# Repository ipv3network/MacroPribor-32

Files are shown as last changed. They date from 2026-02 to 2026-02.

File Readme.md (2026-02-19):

# MacroPribor-32
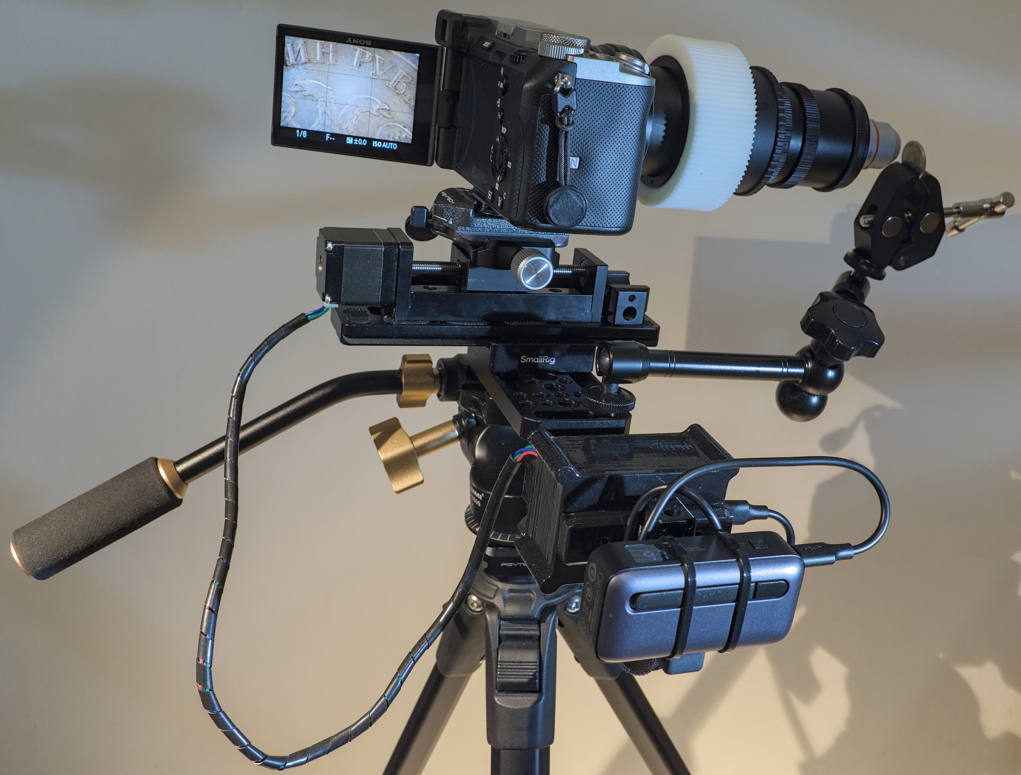
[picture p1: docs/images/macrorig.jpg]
macrorig

Это проект по созданию самодельной моторизованной рейки, облегчающей процесс съемки серий кадров для последующего фокус-стекинга.

Моторизованная направляющая перемещается в заданную начальную точку, сдвигает камеру на небольшие расстояния и посылает камере сигналы для съемки по BLE (Bluetooth Low Energy), пока не достигнет заданной конечной точки. Весь процесс контролируется через встроенный в контроллер веб-интерфейс.

В данный момент поддерживаются только камеры Sony, совместимые с пультом RMT-P1BT (например: A7III, A7V, A7C, A6700, A9III и т.д.).

Код для работы с BLE основан на [https://github.com/coral/freemote](https://github.com/coral/freemote) и [https://github.com/dzwiedziu-nkg/esp32-a7iv-rc](https://github.com/dzwiedziu-nkg/esp32-a7iv-rc).

Всё собрано из недорогих и доступных в продаже компонентов. Корпус с электронными модулями напечатан на 3D-принтере, но при желании (и отсутствии 3D-принтера) можно изготовить корпус альтернативными способами или обойтись вообще без него.

Проект в стадии не очень активной разработки. В будущем планируется разработать нормальный дизайн печатной платы и корпуса, добавить совместимость с другими моделями камер (в том числе по проводному разъему для пульта) и не только это.

## Содержание
* [Инструкция по сборке](#инструкция-по-сборке)
    * [Список компонентов](#список-компонентов)
    * [Сборка электроники](#сборка-электроники)
    * [Сборка корпуса и механических частей](#сборка-корпуса-и-механических-частей)
    * [Установка прошивки](#установка-прошивки)
* [Использование](#использование)
    * [Подключение к камере](#подключение-к-камере)
    * [Настройка сети](#настройка-сети)

# Инструкция по сборке

## Список компонентов
<details>
<summary>Примерный список компонентов на Али с ценами на февраль 2026 года (раскрыть картинку)</summary>
Можно уложиться в 5к рублей.

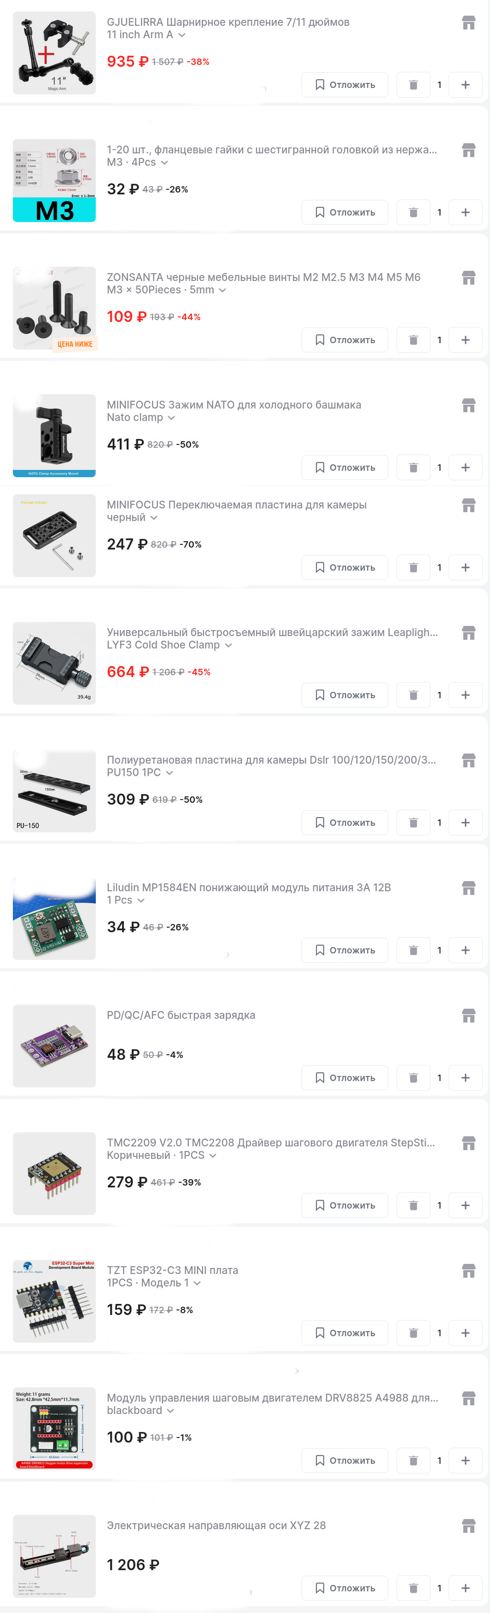
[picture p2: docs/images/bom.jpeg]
bom

</details>

**Электроника** (сложно сказать, по каким ключевым словам конкретные модули найдутся на маркетплейсе, но вы можете визуально ориентироваться по картинкам):
* [Линейная направляющая](./docs/images/rail.jpg) (актуатор) с шаговым двигателем NEMA11, винтовой передачей и рельсовой направляющей. Можно найти в продаже по запросам: "мини направляющая чпу", "электрическая направляющая оси", "линейная направляющая ось чпу" и т.п. Насколько я понимаю, на них стоит дешевый китайский аналог дорогого китайского двигателя MOON'S LE111S-W0601-50-AR1-S-100.
* ESP32-C3 Super Mini (как на схеме ниже).
* Драйвер шагового двигателя (A4988, DRV8825, TMC2209 и т.п.).
* Плата расширения драйвера шагового двигателя (как на схеме ниже).
* Type-C PD/QC триггер (как на схеме ниже).
* Понижающий DC-DC преобразователь MP1584EN или что-то аналогичное.
* Диод Шоттки 1N5819.
* Провода.
* Набор JST коннекторов и обжимка. Но это не обязательно, можно просто припаять провода к платам.

**Крепежные элементы**:
* [Площадка Arca Swiss PU-150](./docs/images/arcaplate.jpg).
* Зажим Arca Swiss, в котором можно просверлить крепежные отверстия под каретку направляющей (смотри схему с размерами ниже).
* Винты М3 для крепления площадки и зажима Arca Swiss к моторизованной направляющей — 8 штук. Длину нужно подобрать эмпирическим путём.
* Гайки М3 — 4 штуки. Лучше с фланцем, но подойдут и обычные.
* Винты для компьютерных корпусных кулеров для сборки 3D-печатного корпуса — 10 штук.
* Сырная пластина, Magic Arm, зажим для NATO rail и прочие необязательные вещи для удобного крепления.
 
## Сборка электроники
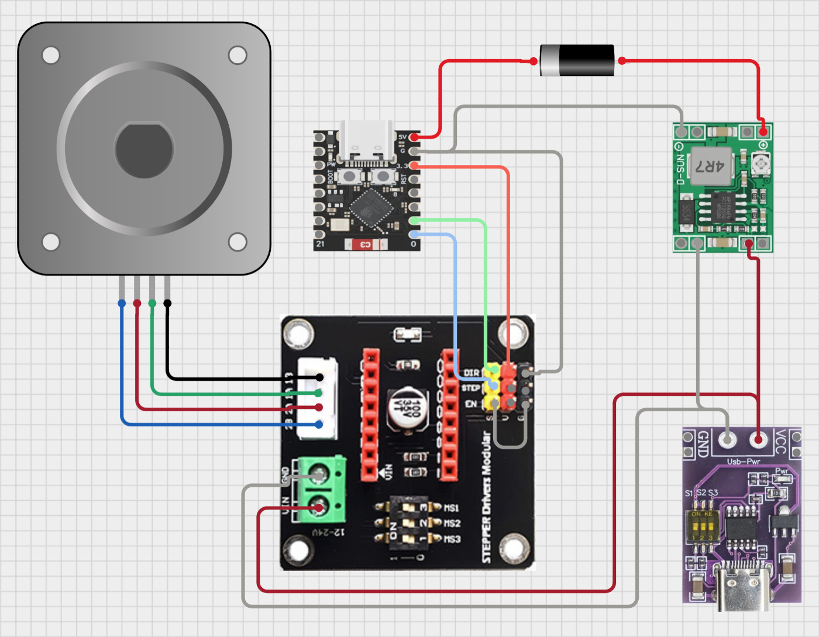
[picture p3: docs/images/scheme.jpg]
scheme

1. Настройте микропереключателями на Type-C PD/QC триггере выходное напряжение в диапазоне от 12В до 20В. Убедитесь, что все нужные блоки питания/зарядные устройства/повербанки выдают нужное напряжение с этими настройками модуля. Некоторые девайсы могут отказаться выдавать определенное напряжение из-за их конструктивных особенностей реализации PD/QC протокола.
2. Подключите выход питания из Type-C триггера ко входу модуля DC-DC преобразователя MP1584EN. 
3. Подайте питание. 
4. Подстроечным резистором настройте на нем выходное напряжение 5В.
5. Отключите питание.
6. Установите драйвер шагового двигателя в плату расширения. Настройте нужные параметры микрошага переключателями на плате расширения. Настройки зависят от модели драйвера, их можно посмотреть в документации драйвера.
7. Замкните перемычкой контакты EN и GND на плате расширения драйвера двигателя.
8. Подключите микроконтроллерный модуль ESP32-C3 к стабилизатору напряжения и драйверу двигателя по схеме.
9. Подключите питание **с отключенным от платы двигателем** и подстроечным резистором на плате драйвера настройте референсное напряжение Vref (напряжение между корпусом подстроечного резистора и GND), соответствующее ограничению тока в 500мА. Ограничение тока вычисляется по формуле из документации, для каждой модели драйвера формула своя. Например, для DRV8825 ``Vref = Current Limit / 2``, т.е. для тока 0.5А значение Vref должно быть 0.25В.
10. Подключите двигатель.

## Сборка корпуса и механических частей
Просверлите отверстия сверлом 3 мм в зажиме и площадке Arca Swiss по размерам со схемы ниже. Прикрутите их к направляющей.
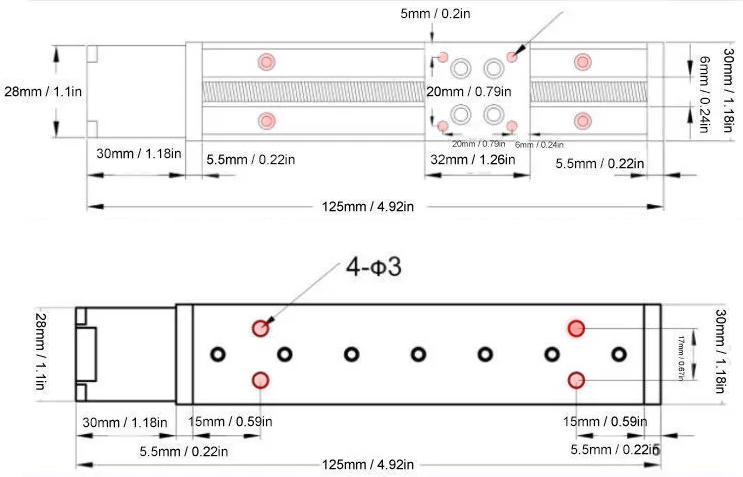
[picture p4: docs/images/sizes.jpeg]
size


У меня был немного неподходящий зажим. Но он уже был, и его не пришлось покупать специально. Поэтому пришлось доработать фрезером.
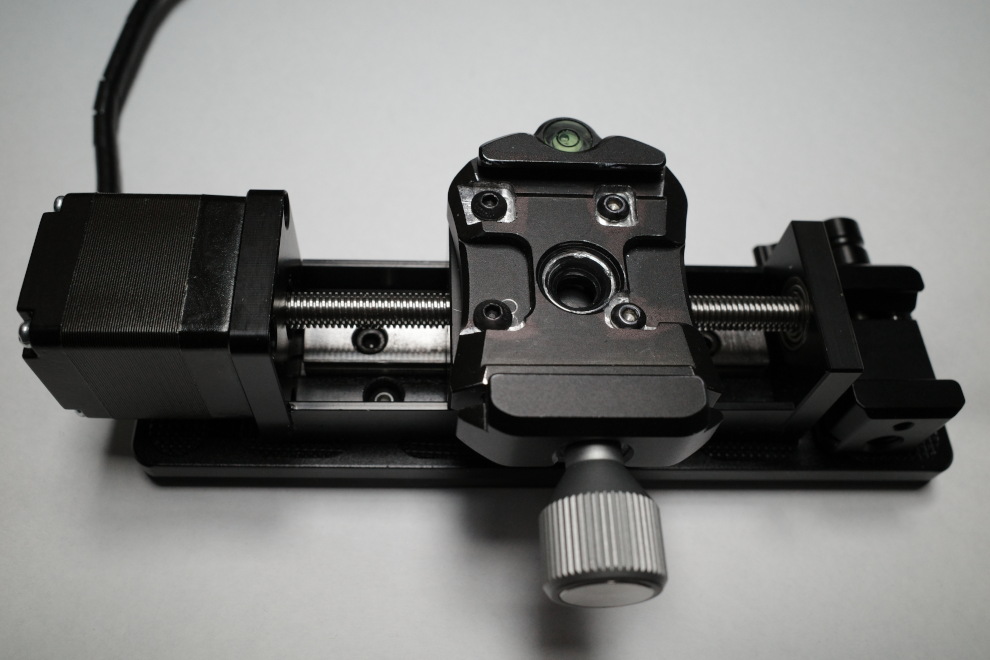
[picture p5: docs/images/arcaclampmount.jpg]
arcaclampmount

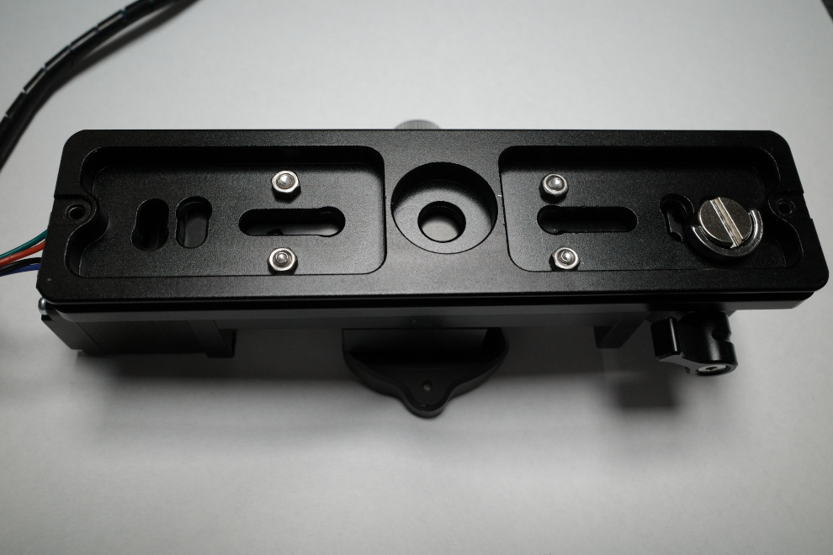
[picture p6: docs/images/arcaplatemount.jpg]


Type-C PD/QC триггер жестко фиксируется в корпусе и прикручивается крышкой с четырьмя винтами от корпусных вентиляторов. Дизайн крепления основан на [этой модели](https://www.printables.com/model/928729-pdqcafc-decoy-trigger-module-enclosure). И провода должны быть припаяны к нему [аналогичным образом](./docs/images/typecdecoy.jpg).

В монтажные отверстия на модулях я запаял JST колодки на плату и обжал на проводах JST разъемы. На гребенку платы для драйвера двигателя установил провода с обжатыми контактами от JST под термоусадкой. После укладки плат зафиксировал их термоклеем. Получилось не очень красиво, но приемлемо.

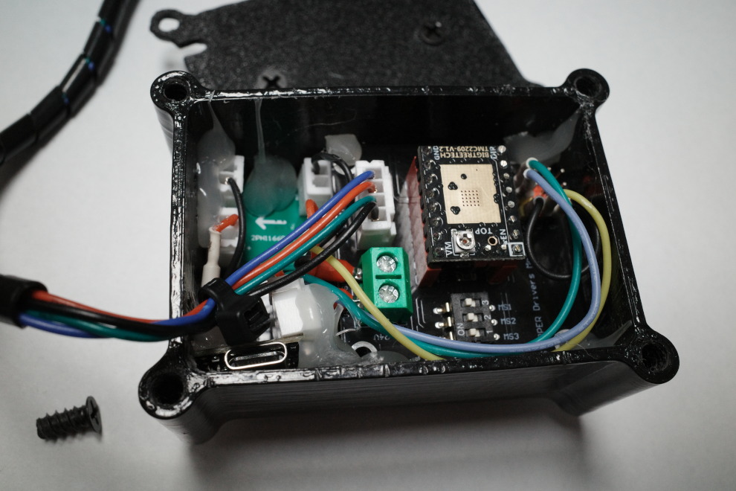
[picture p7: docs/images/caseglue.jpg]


## Установка прошивки
1. Установите PlatformIO и esptool.
2. Отключите питание от Type-C триггера, подключите ESP32-C3 по USB к компьютеру.
3. Можно очистить флеш контроллера:
```bash
pio run --target erase
```
4. В файле ``src/main.cpp`` найдите строку:
```C++
#define CAMERA_NAME "ILCE-7C"  // Имя камеры в Bluetooth меню
```
и замените название модели на вашу.

5. В каталоге со склонированным репозиторием запустите:
```bash
pio run # сборка
pio run --target upload # заливка прошивки
pio run --target uploadfs # заливка файловой системы
```
6. После успешной [настройки сети](#настройка-сети) можно обновлять прошивку по сети через OTA:
```bash
pio run -t clean -e ota
pio run -e ota --target upload
pio run -e ota --target uploadfs
```

# Использование
Интерфейс должен быть интуитивно понятным.

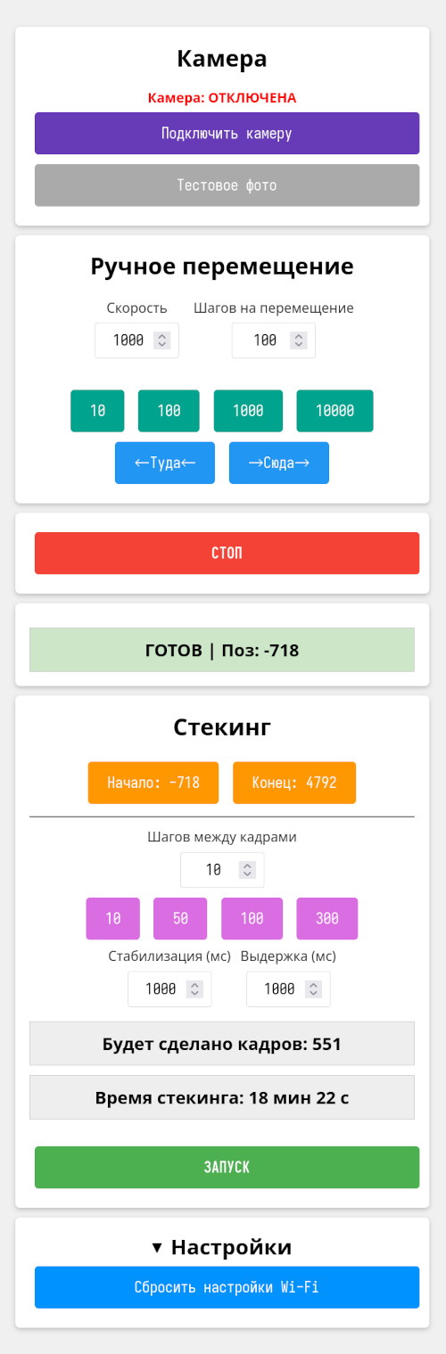
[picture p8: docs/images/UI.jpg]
UI


## Подключение к камере

В меню камеры следуйте инструкции по подключению пульта Sony RMT-P1BT.
Когда в камере запустите "Pairing", в веб-интерфейсе нажмите кнопку "Подключить камеру".

## Настройка сети

При первом включении контроллер поднимает точку доступа с названием "MacroPribor-32" и паролем "MacroPribor-32", если в его памяти до этого не были сохранены данные для подключения к точке доступа (обновление прошивки без предварительной полной очистки флеша не очищает настройки Wi-Fi). Подключайтесь к точке доступа "MacroPribor-32", переходите на её Captive portal [http://192.168.4.1](http://192.168.4.1), настраивайте вашу точку доступа.
Контроллер работает только с точками доступа на 2.4 ГГц, в её сети должен быть DHCP сервер, который выдаст IP адрес контроллеру.

Если нужно принудительно сбросить настройки Wi-Fi -- нажмите кнопку "Сбросить настройки Wi-Fi".

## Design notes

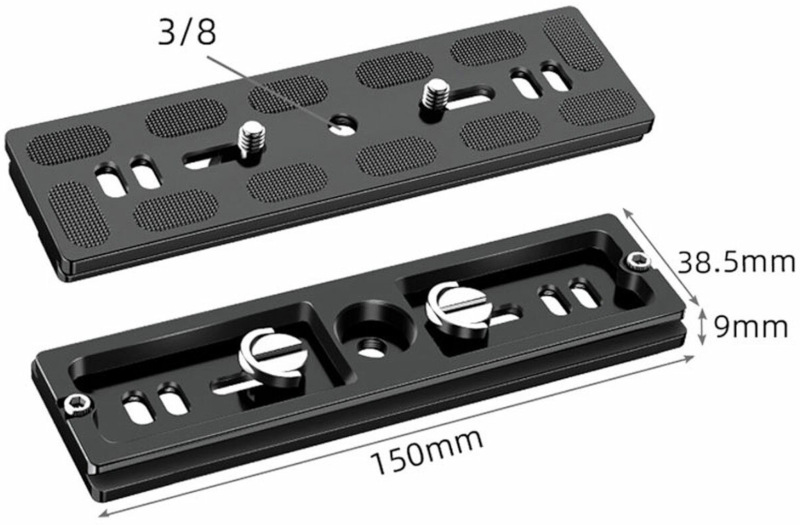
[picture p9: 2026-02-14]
docs/images/arcaplate.jpg

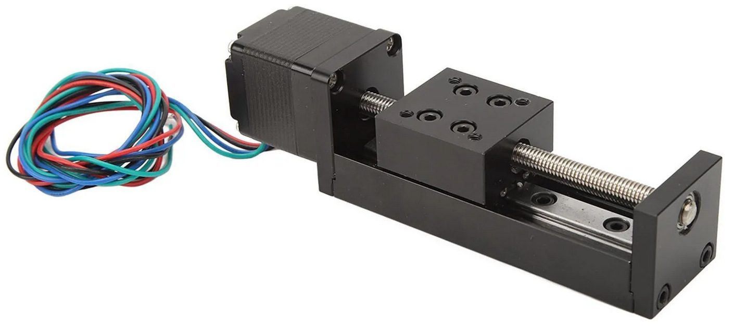
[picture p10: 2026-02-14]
docs/images/rail.jpg

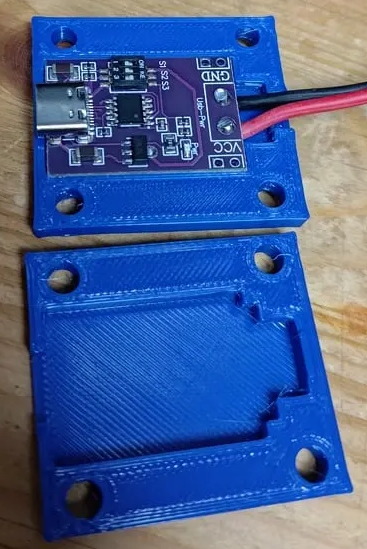
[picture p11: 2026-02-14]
docs/images/typecdecoy.jpg

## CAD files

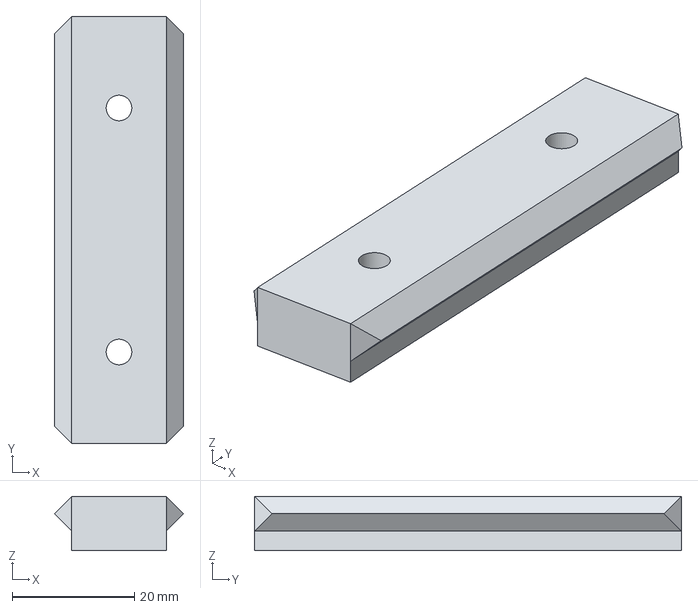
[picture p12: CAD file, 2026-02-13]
3d/electronics_enclosure-rail.step
21.2 x 70.0 x 8.90 mm

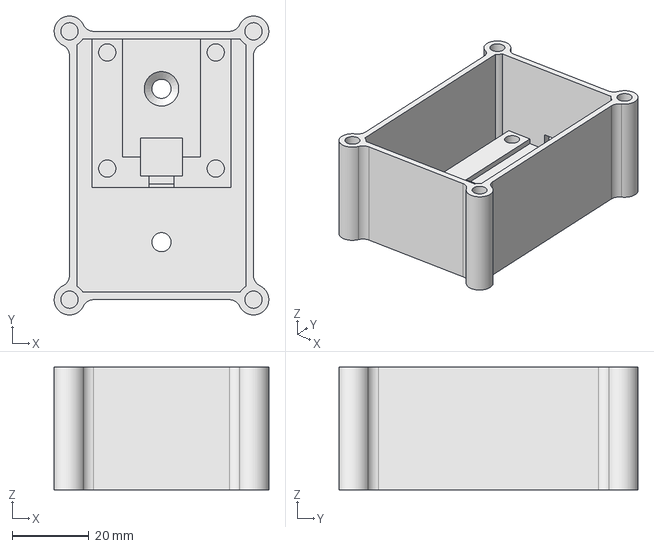
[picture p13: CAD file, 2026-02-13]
3d/electronics_enclosure-Down.step
56.0 x 78.0 x 32.0 mm

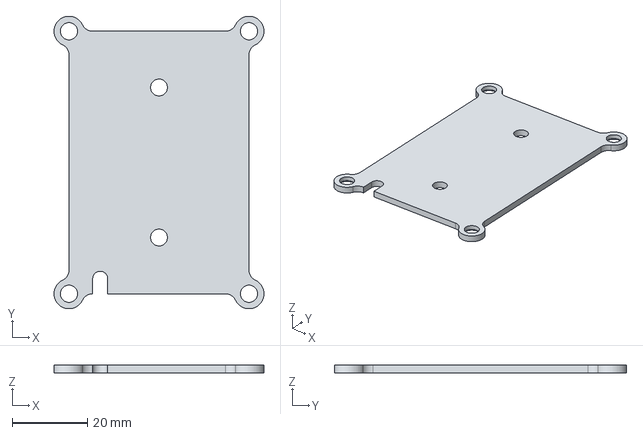
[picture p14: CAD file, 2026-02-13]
3d/electronics_enclosure-Up.step
56.0 x 78.0 x 2.00 mm

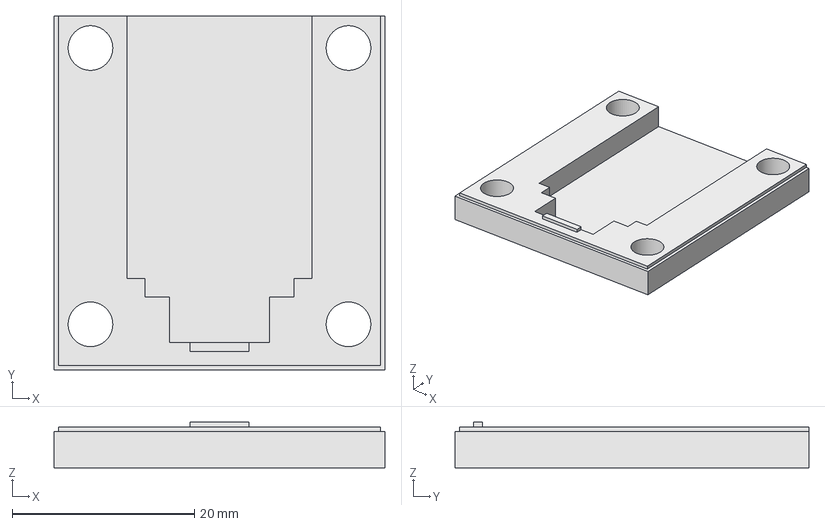
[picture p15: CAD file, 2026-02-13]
3d/electronics_enclosure-decoy_UP.step
36.3 x 38.8 x 5.00 mm

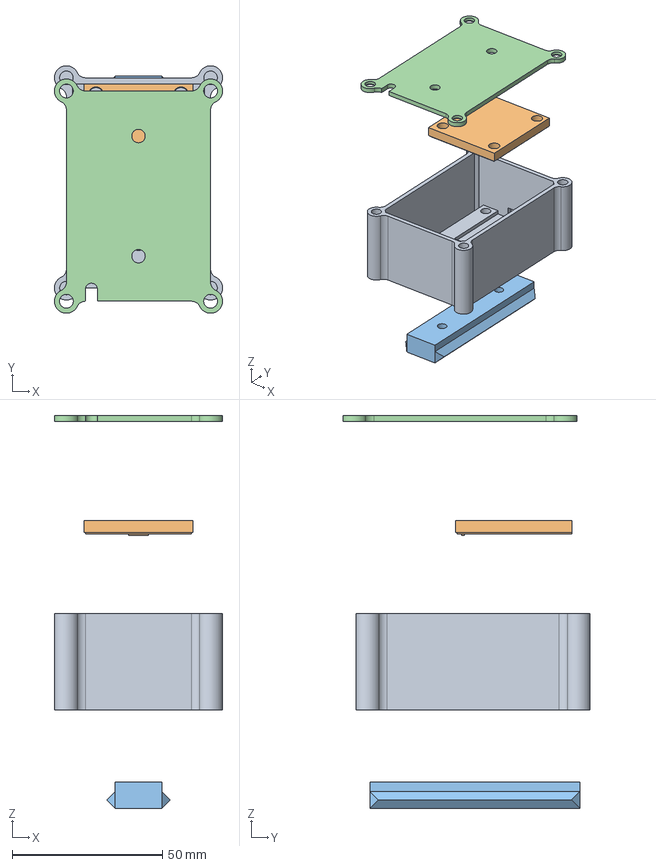
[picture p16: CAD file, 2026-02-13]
3d/electronics_enclosure.FCStd
56.0 x 82.4 x 130.9 mm
Down
decoy_UP
rail
Up

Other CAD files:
3d/electronics_enclosure-Down.stl
3d/electronics_enclosure-Up.stl
3d/electronics_enclosure-decoy_UP.stl
3d/electronics_enclosure-rail.stl

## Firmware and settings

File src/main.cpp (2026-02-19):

#include <WiFi.h>
#include <WiFiUdp.h>
#include <WiFiManager.h>
#include <ArduinoOTA.h>
#include <WebServer.h>
#include <FastAccelStepper.h>
#include <BLEDevice.h>
#include <LittleFS.h>

// ================= НАСТРОЙКИ СЕТИ =================
// Если не удается подключиться к ранее сохраненной точке доступа — поднимаем точку доступа "MacroPribor-32" с паролем "MacroPribor-32"
const char* APssid     = "MacroPribor-32";
const char* APpassword = "MacroPribor-32";
const char* Hostname   = "macropribor-32";

WiFiManager wifiManager;
WebServer      server(80);

// ================= НАСТРОЙКИ BLE (SONY) =================
#define CAMERA_NAME "ILCE-7C"  // Имя камеры в Bluetooth меню

// UUID сервисов Sony
static BLEUUID serviceUUID("8000FF00-FF00-FFFF-FFFF-FFFFFFFFFFFF");
static BLEUUID charCommandUUID((uint16_t)0xFF01);
static BLEUUID charNotifyUUID((uint16_t)0xFF02);

// Команды управления камерой
uint8_t HALF_DOWN[] = {0x01, 0x07};  // Половинное нажатие
uint8_t FULL_DOWN[] = {0x01, 0x09};  // Полное нажатие
uint8_t FULL_UP[]   = {0x01, 0x08};  // Отпустить
uint8_t HALF_UP[]   = {0x01, 0x06};  // Отпустить на половину

// ================= ПИНЫ МОТОРА =================
#define PIN_STEP 0
#define PIN_DIR 1

// ================= НАСТРОЙКИ МЕХАНИКИ =================
#define FIXED_ACCELERATION 1400
#define SPEED 5000

FastAccelStepperEngine engine  = FastAccelStepperEngine();
FastAccelStepper*      stepper = NULL;

// ================= ГЛОБАЛЬНЫЕ ПЕРЕМЕННЫЕ =================
long          pointA           = 0;
long          pointB           = 0;
bool          isStacking       = false;
int           stackState       = 0;
unsigned long stateTimer       = 0;
long          nextPos          = 0;
int           direction        = 1;
int           SHUTTER_PULSE_MS = 200;
uint32_t      last_ota_time    = 0;
bool          otaActive        = false;
// Параметры с веба
long web_speed          = 1000;
long web_stack_step     = 100;
long web_settle_delay   = 1000;
long web_exposure_delay = 1000;

// BLE Переменные
boolean                  bleConnected = false;
boolean                  doConnect    = false;
boolean                  doScan       = false;
BLEAddress*              pServerAddress;
BLERemoteCharacteristic* remoteCommand;
BLERemoteCharacteristic* remoteNotify;
BLEClient*               pClient;

// ================= BLE КЛАССЫ ОБРАТНОЙ СВЯЗИ =================

// Клиент подключился/отключился
class MyClientCallback : public BLEClientCallbacks {
    void onConnect(BLEClient* pclient) { Serial.println("BLE Connected!"); }
    void onDisconnect(BLEClient* pclient) {
        bleConnected = false;
        Serial.println("BLE Disconnected!");
    }
};

// Поиск устройств
class MyAdvertisedDeviceCallbacks : public BLEAdvertisedDeviceCallbacks {
    void onResult(BLEAdvertisedDevice advertisedDevice) {
        Serial.print("BLE Found: ");
        Serial.println(advertisedDevice.getName().c_str());

        // Ищем камеру по имени
        if (advertisedDevice.getName() == CAMERA_NAME) {
            advertisedDevice.getScan()->stop();
            pServerAddress = new BLEAddress(advertisedDevice.getAddress());
            doConnect      = true;
            doScan         = false;
            Serial.println("Camera Found! Ready to connect.");
        }
    }
};

// Спаривание
class MySecurityCallbacks : public BLESecurityCallbacks {
    uint32_t onPassKeyRequest() { return 123456; }
    void     onPassKeyNotify(uint32_t pass_key) {}
    bool     onSecurityRequest() { return true; }
    void     onAuthenticationComplete(esp_ble_auth_cmpl_t cmpl) {
        if (cmpl.success)
            Serial.println("Pairing Success");
        else
            Serial.println("Pairing Failed");
    }
    bool onConfirmPIN(uint32_t pin) { return true; }
};

// ================= ФУНКЦИИ BLE =================

bool connectToCamera() {
    Serial.print("Connecting to ");
    Serial.println(pServerAddress->toString().c_str());

    if (pClient->connect(*pServerAddress)) {
        Serial.println("Connected to server");

        BLERemoteService* pRemoteService = pClient->getService(serviceUUID);
        if (pRemoteService == nullptr) {
            Serial.println("Failed to find service UUID");
            return false;
        }

        remoteCommand = pRemoteService->getCharacteristic(charCommandUUID);
        remoteNotify  = pRemoteService->getCharacteristic(charNotifyUUID);

        if (remoteCommand == nullptr || remoteNotify == nullptr) {
            Serial.println("Failed to find characteristics");
            return false;
        }

        bleConnected = true;
        return true;
    }
    return false;
}

void triggerShutterBLE() {
    if (!bleConnected || remoteCommand == nullptr) return;

    remoteCommand->writeValue(HALF_DOWN, 2, true);
    delay(50);
    remoteCommand->writeValue(FULL_DOWN, 2, true);
}

void releaseShutterBLE() {
    if (!bleConnected || remoteCommand == nullptr) return;

    remoteCommand->writeValue(FULL_UP, 2, true);
    delay(50);
    remoteCommand->writeValue(HALF_UP, 2, true);
}

// ================= ЛОГИКА СЕРВЕРА =================

void handleRoot() {
    File indexHTML = LittleFS.open("/index.html", "r");
    if (!indexHTML) {
        server.send(500, "text/plain", "HTML file not found. Did you run pio run --target uploadfs ?");
        return;
    }

    server.streamFile(indexHTML, "text/html");
    indexHTML.close();
}

void handleState() {
    long framesLeft = 0;
    if (isStacking && web_stack_step > 0) {
        long dist = 0;
        if (direction == 1)
            dist = pointB - stepper->getCurrentPosition();
        else
            dist = stepper->getCurrentPosition() - pointB;
        if (dist < 0) dist = 0;
        framesLeft = dist / web_stack_step;
    }

    // BLE Статус: 0 - откл, 1 - подкл, 2 - поиск
    int bleStatus = 0;
    if (bleConnected)
        bleStatus = 1;
    else if (doScan)
        bleStatus = 2;

    String isRunning   = "0";
    String isMovingToA = "0";
    if (isStacking && stackState != 0) {
        isRunning = "1";
    };
    if (isStacking && stackState == 0) {
        isMovingToA = "1";
    };
    String json = "{";
    json += "\"running\": " + isRunning + ",";
    json += "\"movingA\": " + isMovingToA + ",";
    json += "\"pos\": " + String(stepper->getCurrentPosition()) + ",";
    json += "\"rem\": " + String(framesLeft) + ",";
    json += "\"ble\": " + String(bleStatus) + ",";
    json += "\"pointA\": " + String(pointA) + ",";
    json += "\"pointB\": " + String(pointB);
    json += "}";
    server.send(200, "application/json", json);
}

void handleBLEConnect() {
    if (!bleConnected && !doScan) {
        doScan = true;
        server.send(200, "text/plain", "SCANNING");
    } else {
        server.send(200, "text/plain", "ALREADY ACTIVE");
    }
}

void handleJog() {
    if (isStacking) return;
    web_speed = server.arg("spd").toInt();
    long dist = server.arg("dist").toInt() * server.arg("dir").toInt();
    stepper->setSpeedInHz(web_speed);
    stepper->move(dist);  // относительное перемещение (добавляет к последней целевой позиции)
    server.send(200, "text/plain", "OK");
}

void handleSetA() {
    pointA = stepper->getCurrentPosition();
    server.send(200, "text/plain", "A");
}

void handleSetB() {
    pointB = stepper->getCurrentPosition();
    server.send(200, "text/plain", "B");
}

void handleStartStack() {
    if (isStacking) return;
    web_speed          = server.arg("spd").toInt();
    web_stack_step     = server.arg("step").toInt();
    web_settle_delay   = server.arg("set").toInt();
    web_exposure_delay = server.arg("exp").toInt();

    if (pointB >= pointA)
        direction = 1;
    else
        direction = -1;
    web_stack_step = abs(web_stack_step);

    stepper->setSpeedInHz(web_speed);
    stepper->moveTo(pointA);
    isStacking = true;
    stackState = 0;
    server.send(200, "text/plain", "OK");
}

void handleStop() {
    isStacking = false;
    stepper->stopMove();
    server.send(200, "text/plain", "STOPPED");
}

void handleTestPhoto() {
    triggerShutterBLE();
    delay(200);
    releaseShutterBLE();
    server.send(200, "text/plain", "OK");
}

void handleWifiReset() {
    wifiManager.resetSettings();
    ESP.restart();
}

// ================= SETUP =================
void setup() {
    Serial.begin(115200);

    // WIFI
    wifiManager.setHostname(Hostname);
    wifiManager.autoConnect(APssid, APpassword);
    // OTA
    ArduinoOTA
        .onStart([]() {
            String type;
            otaActive = true;
            if (ArduinoOTA.getCommand() == U_FLASH) {
                type = "sketch";
            } else {  // LittleFS
                type = "filesystem";
            }

            // NOTE: if updating SPIFFS this would be the place to unmount SPIFFS using SPIFFS.end()
            Serial.println("Start updating " + type);
        })
        .onEnd([]() {
            Serial.println("\nEnd");
            otaActive = false;
        })
        .onProgress([](unsigned int progress, unsigned int total) {
            if (millis() - last_ota_time > 500) {
                Serial.printf("Progress: %u%%\n", (progress / (total / 100)));
                last_ota_time = millis();
            }
        })
        .onError([](ota_error_t error) {
            otaActive = false;
            Serial.printf("Error[%u]: ", error);
            if (error == OTA_AUTH_ERROR) {
                Serial.println("Auth Failed");
            } else if (error == OTA_BEGIN_ERROR) {
                Serial.println("Begin Failed");
            } else if (error == OTA_CONNECT_ERROR) {
                Serial.println("Connect Failed");
            } else if (error == OTA_RECEIVE_ERROR) {
                Serial.println("Receive Failed");
            } else if (error == OTA_END_ERROR) {
                Serial.println("End Failed");
            }
        });
    ArduinoOTA.begin();

    // Инициализация FastAccelStepper
    engine.init();
    stepper = engine.stepperConnectToPin(PIN_STEP);
    if (stepper) {
        stepper->setDirectionPin(PIN_DIR);
        stepper->setSpeedInHz(SPEED);
        stepper->setAcceleration(FIXED_ACCELERATION);
        stepper->setCurrentPosition(0);
    }

    // Init BLE Client
    BLEDevice::init("MacroPribor-32");
    BLEDevice::setEncryptionLevel(ESP_BLE_SEC_ENCRYPT);
    BLEDevice::setSecurityCallbacks(new MySecurityCallbacks());
    pClient = BLEDevice::createClient();
    pClient->setClientCallbacks(new MyClientCallback());

    // Инициализируем ФС
    if (!LittleFS.begin(true)) {
        Serial.println("LittleFS mount failed!");
        return;
    }

    // Веб сервер
    server.on("/", handleRoot);
    server.on("/state", handleState);
    server.on("/ble_connect", handleBLEConnect);
    server.on("/jog", handleJog);
    server.on("/setA", handleSetA);
    server.on("/setB", handleSetB);
    server.on("/start_stack", handleStartStack);
    server.on("/stop", handleStop);
    server.on("/wifi", handleWifiReset);
    server.on("/test_photo", handleTestPhoto);
    server.begin();
}

// ================= LOOP =================
void loop() {
    server.handleClient();
    if (otaActive) {
        ArduinoOTA.handle();  // вызываем каждый проход, пока идёт обновление
    } else {
        static unsigned long lastOta = 0;
        if (millis() - lastOta > 50) {  // вызываем реже, если обновление не активно
            lastOta = millis();
            ArduinoOTA.handle();
        }
    }

    // --- ОБРАБОТКА BLE ---
    if (doScan) {
        BLEScan* pBLEScan = BLEDevice::getScan();
        pBLEScan->setAdvertisedDeviceCallbacks(new MyAdvertisedDeviceCallbacks());
        pBLEScan->setActiveScan(true);
        pBLEScan->start(5, false);
        if (!doConnect) {
            doScan = false;
            Serial.println("Scan finished, camera not found.");
        }
    }

    if (doConnect) {
        if (connectToCamera()) {
            Serial.println("Success connection!");
        } else {
            Serial.println("Failed connection.");
        }
        doConnect = false;
    }

    // Стекинг
    if (isStacking) {
        switch (stackState) {
            // 0: Возврат к старту
            case 0:
                if (!stepper->isRunning()) {
                    delay(100);
                    nextPos    = pointA;
                    stackState = 1;
                }
                break;

            // 1: Движение к позиции кадра
            case 1:
                if ((direction == 1 && stepper->getCurrentPosition() >= pointB) || (direction == -1 && stepper->getCurrentPosition() <= pointB)) {
                    isStacking = false;
                } else {
                    if (!stepper->isRunning()) {
                        stateTimer = millis();
                        stackState = 2;
                    }
                }
                break;

            // 2: Стабилизация и спуск
            case 2:
                if (millis() - stateTimer > web_settle_delay) {
                    triggerShutterBLE();
                    stateTimer = millis();
                    stackState = 3;
                }
                break;

            // 3: Выдержка и отпускание
            case 3:
                if (millis() - stateTimer > SHUTTER_PULSE_MS) {
                    releaseShutterBLE();
                    stateTimer = millis();
                    stackState = 4;
                }
                break;

            // 4: Ожидание выдержки
            case 4:
                if (millis() - stateTimer > web_exposure_delay) {
                    nextPos = stepper->getCurrentPosition() + (web_stack_step * direction);
                    stepper->moveTo(nextPos);
                    stackState = 1;
                }
                break;
        }
    }
}

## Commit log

2026-02-13 Добавил код
2026-02-13 Добавил 3d модели корпуса и platformio.ini
    [electronics_enclosure-Down.step, electronics_enclosure-Down.stl, electronics_enclosure-Up.step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]
2026-02-14 Добавил документацию
2026-02-14 придумал название проекта, дописал документацию, внес мелкие правки в код
2026-02-14 поправил опечатку в инструкции
2026-02-14 добавил фото, сделал некоторые косметические правки
2026-02-17 Перешел на FastAccelStepper, доработки веб-интерфейса
2026-02-17 мелкие правки для красоты
2026-02-17 поправил Readme
2026-02-19 добавил новую таблицу разделов, убрал wifimanager
    [partitions.csv]
2026-02-19 добавил поддержку OTA
2026-02-19 доработал настройки ota
2026-02-19 вернулся к wifimanager
2026-02-19 Доработал сброс настроек wifi, поправил настройки platformio
2026-02-19 Обновил README
2026-02-19 Обновил скриншот интерфейса
2026-02-19 микрофикс разметки
2026-02-19 удалил лишний код
2026-02-19 микроправки в коде стекинга
2026-02-20 добавил лицензию
